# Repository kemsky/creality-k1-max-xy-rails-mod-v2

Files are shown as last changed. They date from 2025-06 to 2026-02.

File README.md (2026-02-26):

# Creality `K1 Max` XY Rails Mod V2

## Description

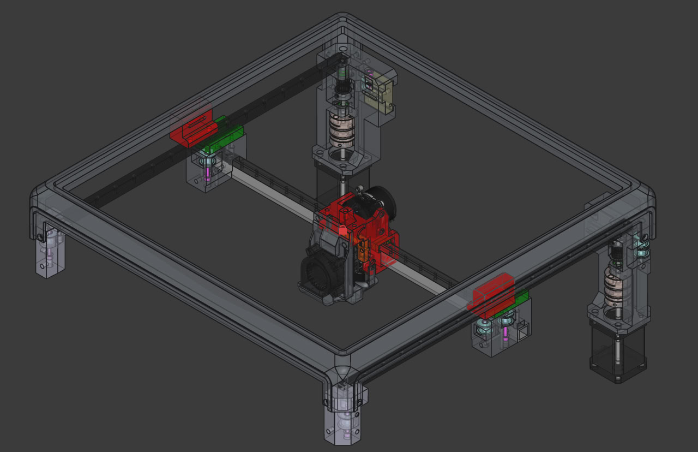
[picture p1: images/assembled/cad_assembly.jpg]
CAD


The primary difference from the previous version is MGN9 rail on X axis, it makes X axis lighter and increases maximum accelerations. Also, it includes all improvements made for regular K1.

This mod fixes `K1 Max` issues namely excessive ringing/echo, unstable print quality, frequent maintenance, also it makes printer quiet.

- **This mod does not change print area (almost, clr_noz_start_y: 297)**
- **You must use camera mount from this mod**
- **You must remove stock motor pulleys (or use non-stock stepper motors)**

### Belts, pulleys, motors

This mode uses `POWGE` 7.7 mm belt and corresponding idler pulleys. You can use 6 mm belt and stock idlers if you add washers to compensate height differences (`POWGE` idlers have 10.4 mm height). Also, you can use `F604ZZ` flanged bearings (4x12x4) and 2mm washers instead of `POWGE` pulleys.

You have to remove stock motor pulleys. You can use a bearing puller to do that (some people use printed pullers e.g. [pulley puller](https://www.printables.com/model/515503-pulley-puller)). If pulleys sit too tight you can use dremel and make cuts to relax pulleys. you have to be careful to avoid damage to motor shafts

I used 20T motor pulleys for 15 mm belt (`rotation_distance` needs to be adjusted to `40` and `driver_SGTHRS` must be tuned `printer.cfg`).

You can install non-stock motors e.g. `Leadshine 42cm06 1.8` (low VFA, silent, high torque, custom wiring needed) or `LDO-42STH48-1684MAC 0.9` (requires `full_steps_per_rotation: 400`, loud, limited acceleration, low VFA).

<details>
    <summary>Leadshine 42cm06 1.8 wiring</summary>
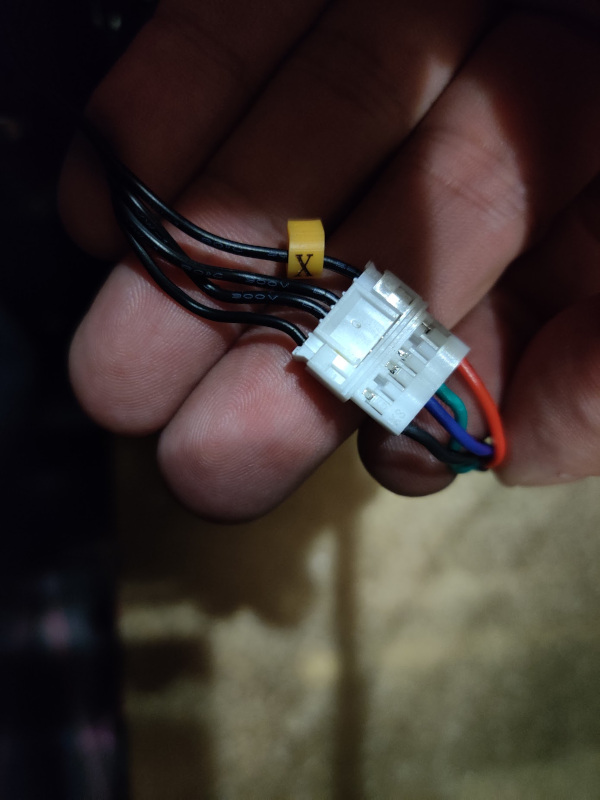
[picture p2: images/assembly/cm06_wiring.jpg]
    
</details>
<br>

This mod uses double diaphragm couplers and `MF95ZZ` bearings.

#### Belts tuning

Preferred way is to use Spectroid android app (or any other program that can show sound frequency).

Move toolhead to the middle, move X axis to have 150mm between motor mounts and XY joints.

Pluck the shortest belt on each side, displayed frequency should be the same. Target frequency is 120-130Hz, if you go higher than 130Hz you risk to damage belts.

#### Linear rails

This mod uses two `MGN12` rails with `MGN12H` carriages for Y and one `MGN9` rail with `MGN9H` carriage for X axis.

X rail has max length of 410 mm, 380 mm between far left and far right holes. X axis requires 15x15x2 mm aluminium tube (the same length as rail). It is important to use quality rails for X axis (with minimal backlash, Z1 preload).

Y rails have max length of 385 mm (375 + 5x2 mm), 375 mm between far left and far right holes.

#### Materials

Recommended printing materials are PA-GF, PA-CF, ABS-GF, ABS-CF or anything else that is rigid and can sustain high temperatures. Screw joints tend to become loose in ABS over time.

Wall loops, top/bottom layers should be at least 5, I'd recommend 6-7, infill 40%, add manual normal supports.

<details>
    <summary>Printing orientation</summary>
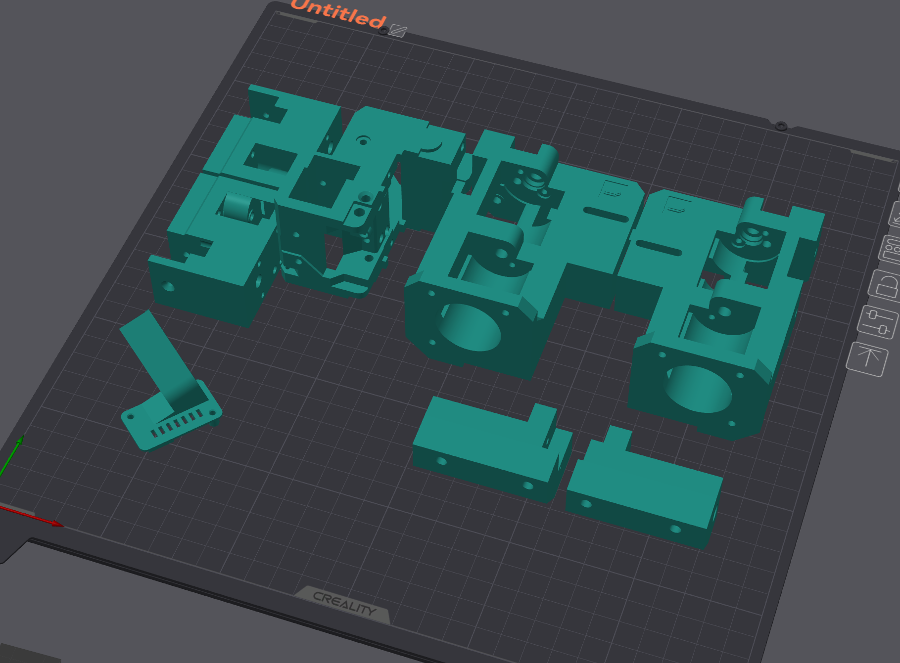
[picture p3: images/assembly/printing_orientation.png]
    
</details>

#### Options for maximum performance

- Use light extruder - [KKm extruder](https://www.printables.com/model/906070-artis3d-kkm-extruder-remix)

## License

All work in this repository falls under the Attribution-NonCommercial-ShareAlike 4.0 International (CC BY-NC-SA 4.0).

<https://creativecommons.org/licenses/by-nc-sa/4.0/>

### Notes

Partially this work is based on [creality-k1-xy-rails-mod](https://github.com/kemsky/creality-k1-xy-rails-mod) and uses some CAD files made by [Henlor](https://www.printables.com/@Henlor).

## Published

<https://www.printables.com/model/1339635-creality-k1-max-xy-linear-rails-mod-v2>

<!-- 
https://www.thingiverse.com/thing:6893994

https://makerworld.com/en/models/931135 -->

## Photos

<details>
    <summary>Photo 1</summary>
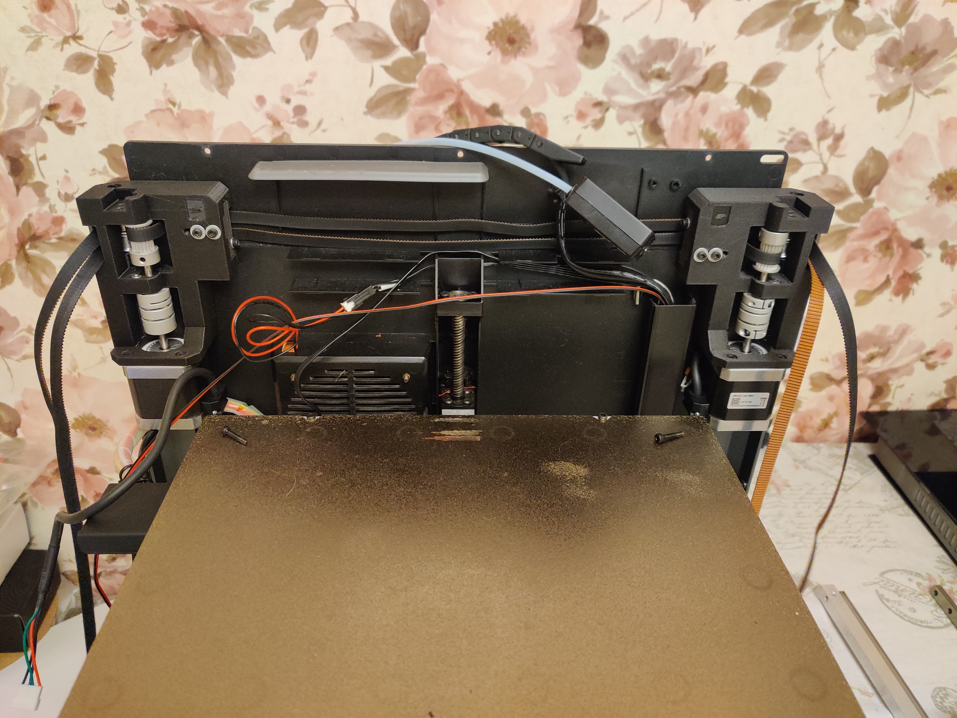
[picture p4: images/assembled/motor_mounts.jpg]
    
</details>

<details>
    <summary>Photo 2</summary>
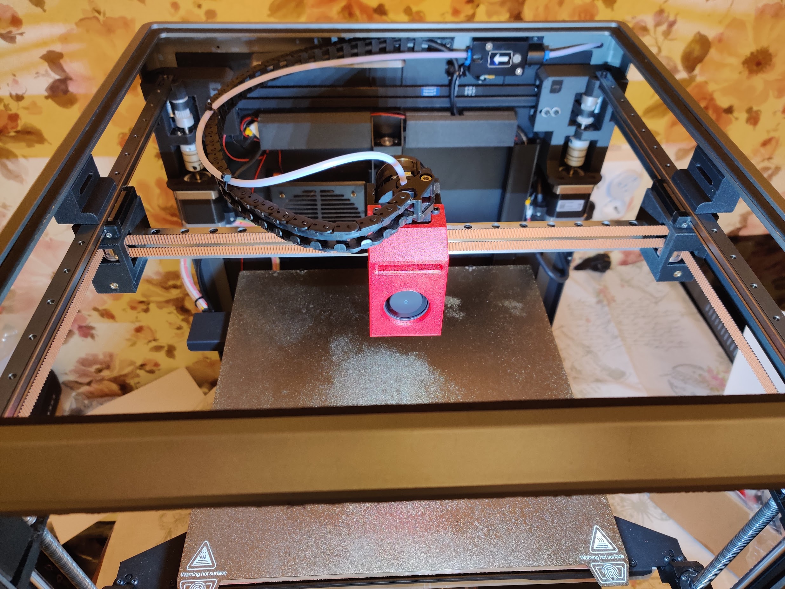
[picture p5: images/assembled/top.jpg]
    
</details>

## BOM, Assembly

! `Flat Thin Wafer Head Screw` - M3 screws with flat head that has 1 mm thickness.
You can find those on AliExpress, manufacturer NINDEJIN, search for "Ultra Low Profile Head Screw".

### Camera

<details>
    <summary>Preview</summary>
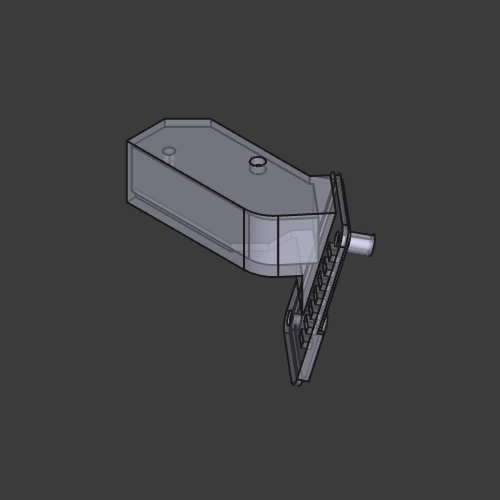
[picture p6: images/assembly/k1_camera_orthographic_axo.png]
k1_camera.stl
    
</details>
<br>

[k1_camera.stl](/stl/k1_camera.stl)

### Front idler left

<details>
    <summary>Preview</summary>
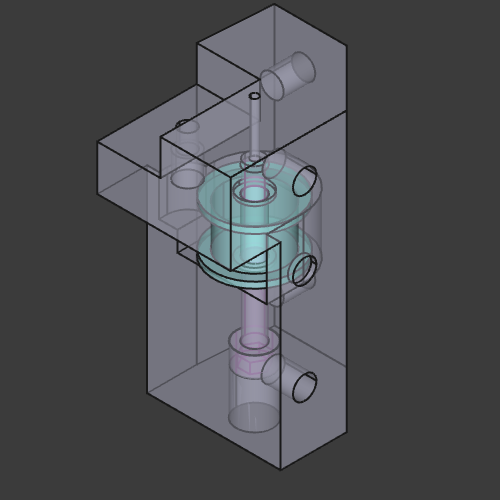
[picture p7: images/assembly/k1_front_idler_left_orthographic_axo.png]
front_idler_left.stl
    
</details>
<br>

[front_idler_left.stl](/stl/k1_front_idler_left.stl)

| Item | Type | Count |
|---|---|---|
| DIN 912 Socket Head Cap Screw | M4 30 mm  | 1 |
| DIN 7991 Flat Head Cap Screw | M3 6 mm | 4 |
| DIN 912 Socket Head Cap Screw | M3 16 mm  | 1 |
| POWGE GT2 No Teeth Idler Pulley | 7.7 mm | 1 |
| Heat insert | M3 5x5 mm | 5 |

### Front idler right

<details>
    <summary>Preview</summary>
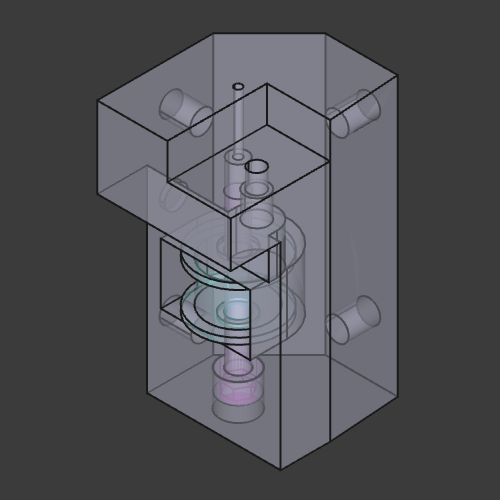
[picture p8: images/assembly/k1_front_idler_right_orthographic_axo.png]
front_idler_right.stl
    
</details>
<br>

[front_idler_right.stl](/stl/k1_front_idler_right.stl)

| Item | Type | Count |
|---|---|---|
| DIN 912 Socket Head Cap Screw | M4 30 mm  | 1 |
| DIN 7991 Flat Head Cap Screw | M3 6 mm | 4 |
| DIN 912 Socket Head Cap Screw | M3 16 mm  | 1 |
| POWGE GT2 No Teeth Idler Pulley | 7.7 mm | 1 |
| Heat insert | M3 5x5 mm | 5 |

### Joint left

<details>
    <summary>Preview</summary>
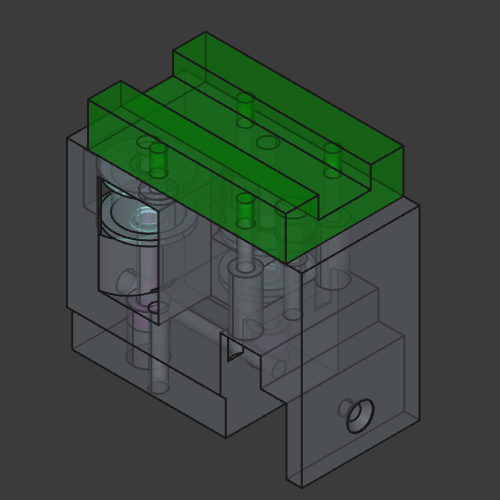
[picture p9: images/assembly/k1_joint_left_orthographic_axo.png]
k1_joint_left.stl
    
</details>
<br>

[k1_joint_left.stl](/stl/k1_joint_left.stl)

| Item | Type | Count |
|---|---|---|
| DIN 912 Socket Head Cap Screw | M4 30 mm | 2 |
| DIN 7991 Flat Head Cap Screw | M3 52 mm | 1 |
| Flat Thin Wafer Head Screw | M3 6 mm | 1 |
| DIN 912 Socket Head Cap Screw | M3 12 mm | 3 |
| DIN 912 Socket Head Cap Screw | M3 25 mm | 1 |
| POWGE GT2 No Teeth Idler Pulley | 7.7 mm | 2 |
| MGN12H block | | 1 |
| Heat insert | M3 4.5x5 mm | 1 |
| Heat insert | M3 5x7 mm | 1 |

### Joint right

<details>
    <summary>Preview</summary>
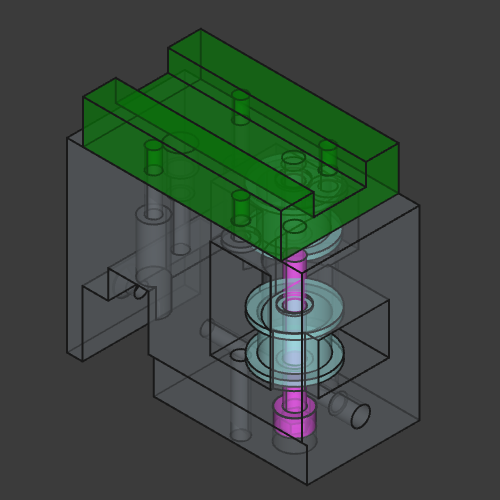
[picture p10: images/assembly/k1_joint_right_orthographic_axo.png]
k1_joint_right.stl
    
</details>
<br>

[k1_joint_right.stl](/stl/k1_joint_right.stl)

| Item | Type | Count |
|---|---|---|
| DIN 912 Socket Head Cap Screw | M4 30 mm | 2 |
| DIN 7991 Flat Head Cap Screw | M3 52 mm | 1 |
| Flat Thin Wafer Head Screw | M3 6 mm | 2 |
| DIN 912 Socket Head Cap Screw | M3 12 mm | 2 |
| DIN 912 Socket Head Cap Screw | M3 25 mm | 1 |
| POWGE GT2 No Teeth Idler Pulley | 7.7 mm | 2 |
| MGN12H block | | 1 |
| Heat insert | M3 4.5x5 mm | 1 |
| Heat insert | M3 5x7 mm | 1 |

### Y rail mounts

<details>
    <summary>Preview</summary>
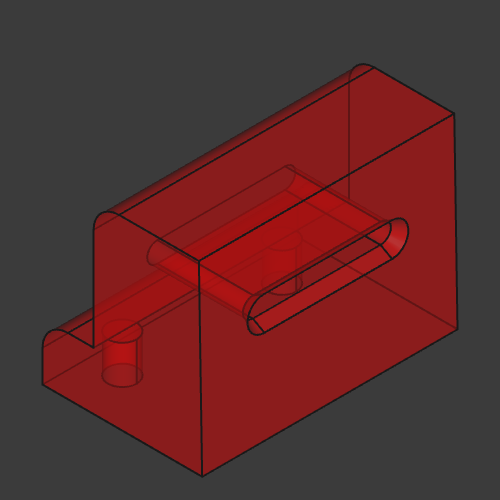
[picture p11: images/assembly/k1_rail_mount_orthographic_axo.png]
k1_rail_mount.stl
    
</details>
<br>

[k1_rail_mount.stl](/stl/k1_rail_mount.stl) x2

| Item | Type | Count |
|---|---|---|
| DIN 912 Socket Head Cap Screw | M3 25 mm  | 2 |
| DIN 912 Socket Head Cap Screw | M3 8 mm | 4 |
| Heat insert | M3 5x5 mm | 4 |

Mounting Y rails to the top frame is important if you want less vibrations.

### Y axis

See [cad_rail_mgn12.FCStd](/src/cad_rail_mgn12.FCStd) for exact configuration and dimensions.

| Item | Type | Count |
|---|---|---|
| MGN12 linear rail | 385 mm | 2 |

Y rails have max length of 385 mm (375 + 5x2 mm), 375 mm between far left and far right holes. `MGN12H` carriage.

### X axis

See [cad_x_axis.FCStd](/src/cad_x_axis.FCStd) for exact configuration and dimensions.

First, make two holes on the left and on the right, tap M3 threads, mount MGN9 rail, align it carefully and tighten screws. Use rail as drilling template, make mark using 4 mm drill bit, then drill remaining holes using 2.5 mm drill bit, then tap M3 threads.

| Item | Type | Count |
|---|---|---|
| Aluminium square pipe | 15x15x2 410 mm | 1 |
| DIN 912 Socket Head Cap Screw | M3 6 mm | 9-18  |
| MGN9 linear rail | 410 mm | 1 |

X rail has max length of 410 mm, 380 mm between far left and far right holes. X axis requires 15x15x2 mm aluminium tube (the same length as rail). `MGN9H` carriage.

It is important to use quality rails for X axis (with minimal backlash, Z1 preload).

### Tensioner left

<details>
    <summary>Preview</summary>
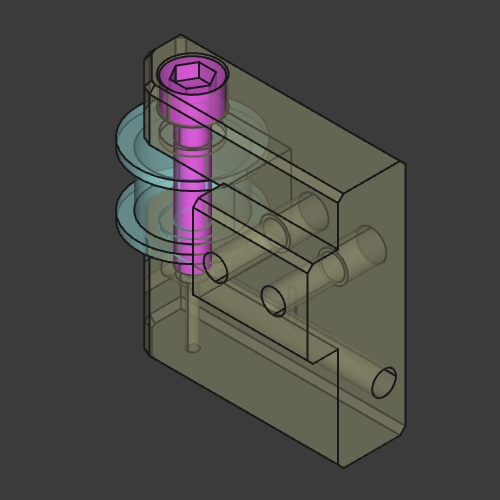
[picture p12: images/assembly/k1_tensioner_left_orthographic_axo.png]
k1_tensioner_left.stl
    
</details>
<br>

[k1_tensioner_left.stl](/stl/k1_tensioner_left.stl)

| Item | Type | Count |
|---|---|---|
| DIN 912 Socket Head Cap Screw | M3 45 mm | 1 |
| DIN 912 Socket Head Cap Screw | M3 16 mm | 2 |
| DIN 912 Socket Head Cap Screw | M4 20 mm | 1 |
| Washer/Gasket | M3 | 2 |
| POWGE GT2 No Teeth Idler Pulley | 7.7 mm | 1 |
| Heat insert | M3 4.5x3 mm | 2 |

### Tensioner right

<details>
    <summary>Preview</summary>
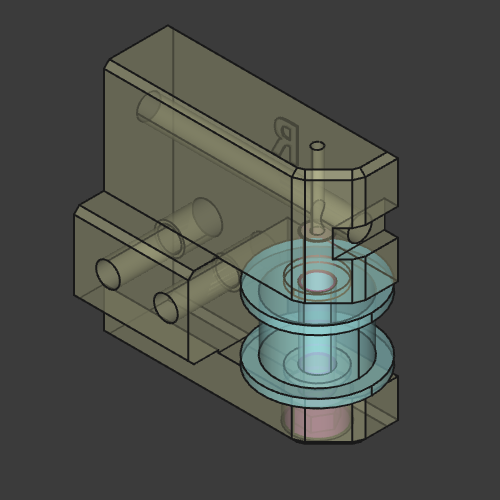
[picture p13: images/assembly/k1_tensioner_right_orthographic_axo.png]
k1_tensioner_right.stl
    
</details>
<br>

[k1_tensioner_right.stl](/stl/k1_tensioner_right.stl)

| Item | Type | Count |
|---|---|---|
| DIN 912 Socket Head Cap Screw | M3 45 mm | 1 |
| DIN 912 Socket Head Cap Screw | M3 16 mm | 2 |
| DIN 912 Socket Head Cap Screw | M4 20 mm | 1 |
| Washer/Gasket | M3 | 2 |
| POWGE GT2 No Teeth Idler Pulley | 7.7 mm | 1 |
| Heat insert | M3 4.5x3 mm | 2 |

### Motor mount left

<details>
    <summary>Preview</summary>
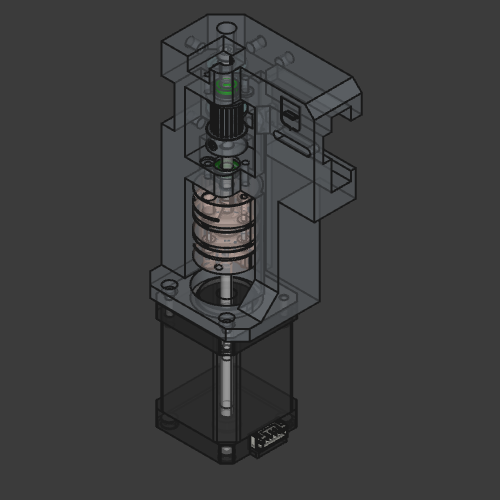
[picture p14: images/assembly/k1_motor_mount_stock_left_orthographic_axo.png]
k1_motor_mount_stock_left.stl
    
</details>
<br>

- For stock motors - [k1_motor_mount_stock_left.stl](/stl/k1_motor_mount_stock_left.stl)
- For non-stock motors - [k1_motor_mount_left.stl](/stl/k1_motor_mount_left.stl)

| Item | Type | Count |
|---|---|---|
| DIN 7991 Flat Head Cap Screw | M3 6 mm | 4 |
| DIN 912 Socket Head Cap Screw | M3 6 mm | 3 |
| DIN 912 Socket Head Cap Screw | M3 16 mm  | 1 |
| Flat Thin Wafer Head Screw | M3 6 mm | 2 |
| MF95ZZ Bearing | | 2 |
| Double Diaphragm Coupler | 20x30 5x5 | 1 |
| Shaft | 5x57 mm | 1 |
| Motor Pulley for 15mm belt | 20T 5 mm  | 1 |
| POWGE GT2 No Teeth Idler Pulley | 7.7 mm | 2 |
| Heat insert | M3 5x5 mm | 6 |

You'll need 1 M3x35 screw from stock gantry motor mounts and 1 M3 5x7 mm heat insert, alternatively you can use M4x35 SHCS screw.

### Motor mount right

<details>
    <summary>Preview</summary>
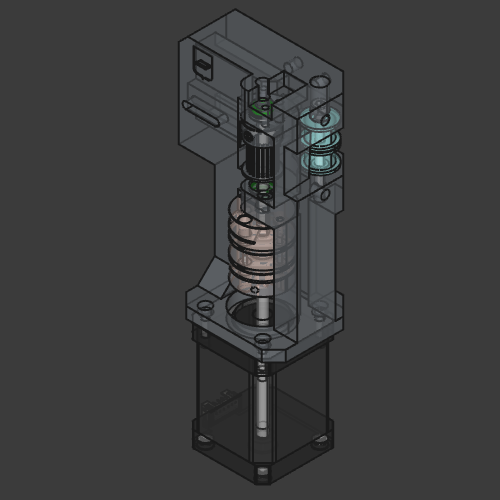
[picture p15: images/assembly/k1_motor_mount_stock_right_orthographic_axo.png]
k1_motor_mount_stock_right.stl
    
</details>
<br>

- For stock motors - [k1_motor_mount_stock_right.stl](/stl/k1_motor_mount_stock_right.stl)
- For non-stock motors - [k1_motor_mount_right.stl](/stl/k1_motor_mount_right.stl)

| Item | Type | Count |
|---|---|---|
| DIN 7991 Flat Head Cap Screw | M3 6 mm | 4 |
| DIN 912 Socket Head Cap Screw | M3 6 mm | 3 |
| DIN 912 Socket Head Cap Screw | M3 16 mm  | 1 |
| Flat Thin Wafer Head Screw | M3 6 mm | 2 |
| MF95ZZ Bearing | | 2 |
| Double Diaphragm Coupler | 20x30 5x5 | 1 |
| Shaft | 5x57 mm | 1 |
| Motor Pulley for 15mm belt | 20T 5 mm  | 1 |
| POWGE GT2 No Teeth Idler Pulley | 7.7 mm | 2 |
| Heat insert | M3 5x5 mm | 6 |

You'll need 1 M3x35 screw from stock gantry motor mounts and 1 M3 5x7 mm heat insert, alternatively you can use M4x35 SHCS screw.

### Toolhead clamp left

<details>
    <summary>Preview</summary>
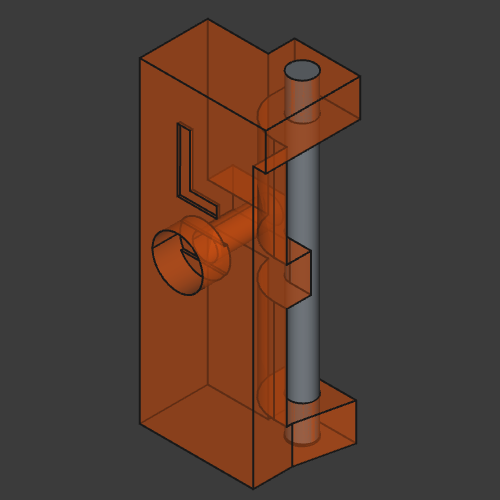
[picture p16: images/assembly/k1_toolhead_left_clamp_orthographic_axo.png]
k1_toolhead_left_clamp.stl
    
</details>
<br>

[k1_toolhead_left_clamp.stl](/stl/k1_toolhead_left_clamp.stl)

| Item | Type | Count |
|---|---|---|
| DIN 912 Socket Head Cap Screw | M2 10 mm | 1 |
| Shaft | 2x25 mm | 1 |

### Toolhead clamp right

<details>
    <summary>Preview</summary>
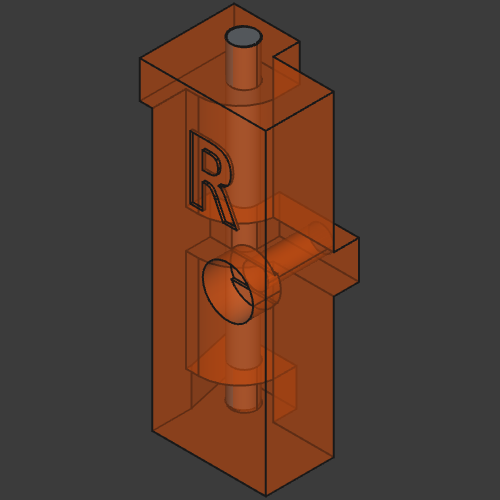
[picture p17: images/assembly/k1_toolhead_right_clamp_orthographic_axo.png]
k1_toolhead_right_clamp.stl
    
</details>
<br>

[k1_toolhead_right_clamp.stl](/stl/k1_toolhead_right_clamp.stl)

| Item | Type | Count |
|---|---|---|
| DIN 912 Socket Head Cap Screw | M2 10 mm | 1 |
| Shaft | 2x25 mm | 1 |

### Toolhead fan spacer

<details>
    <summary>Preview</summary>
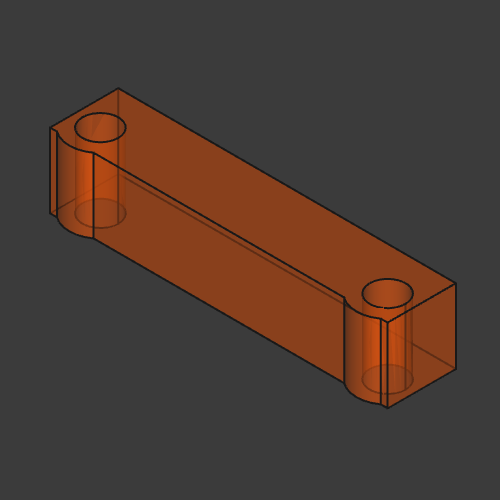
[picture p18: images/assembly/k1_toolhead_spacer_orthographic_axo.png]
k1_toolhead_spacer.stl
    
</details>
<br>

Regular hotend - [k1_toolhead_spacer.stl](/stl/k1_toolhead_spacer.stl)

Unicorn hotend - [k1_toolhead_spacer_unicorn.stl](/stl/k1_toolhead_spacer_unicorn.stl)

### Toolhead

<details>
    <summary>Preview</summary>
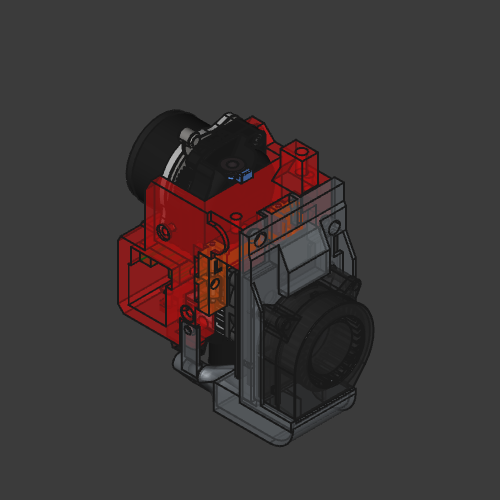
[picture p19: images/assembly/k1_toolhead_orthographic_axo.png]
k1_toolhead.stl
    
</details>
<br>

[k1_toolhead.stl](/stl/k1_toolhead.stl)

| Item | Type | Count |
|---|---|---|
| Flat Thin Wafer Head Screw | M3 6 mm | 4 |
| Flat Thin Wafer Head Screw | M3 8 mm | 3 |
| DIN 912 Socket Head Cap Screw | M2 12 mm | 1 |
| MGN9H block | | 1 |
| Heat insert | M3 4.5x3 mm | 6 |
| Heat insert | M3 5x7 mm | 1 |
| Heat insert | M3 5x4 mm | 4 |
| Heat insert | M2 3.5x3 mm | 4 |

#### Toolhead Microprobe

| Item | Type | Count |
|---|---|---|
| Heat insert | M2.5 3.5x4 mm | 2 |

You can install `BIQU MicroProbe` sensor which is much better than original load cell probe.

[ **!** ] Pins on toolhead board ("touch" connector) do not match microprobe pins, you can not use premade JST 1.25 5pins cable, you'll have to make your own.

<details>
    <summary>Pins</summary>
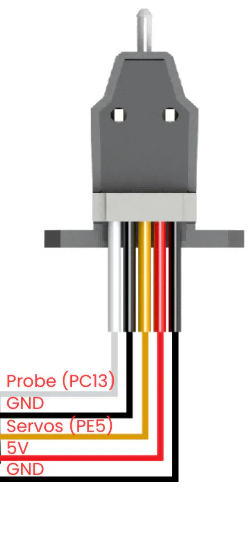
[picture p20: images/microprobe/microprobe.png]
microprobe
    
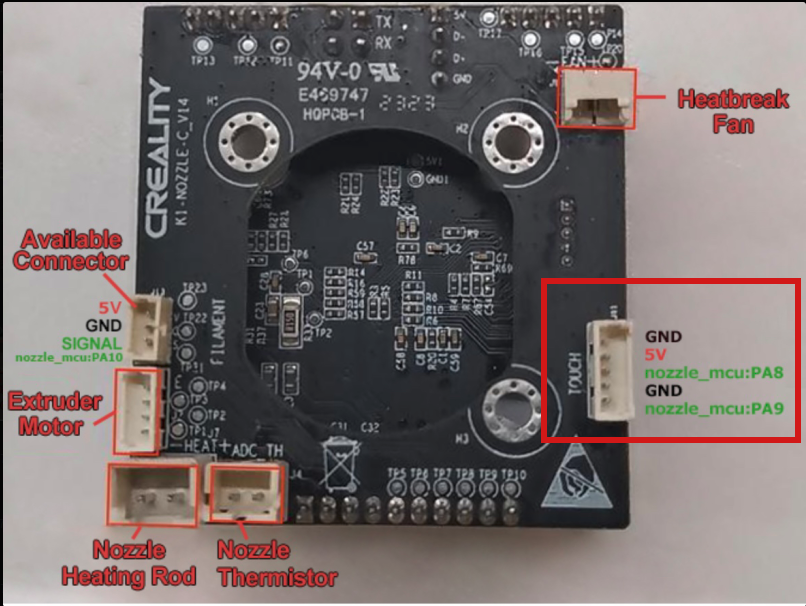
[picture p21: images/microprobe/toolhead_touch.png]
toolhead_touch
    
</details>
<br>

```pre
- touch GND            -> microprobe GND    (black)
- touch 5v             -> microprobe 5v     (red)
- touch nozzle_mcu:PA8 -> microprobe servo  (yellow)
- touch GND            -> microprobe GND    (black)
- touch nozzle_mcu:PA9 -> microprobe probe  (white)
```

1. Remove all `prtouch` sections from `printer.cfg`
2. Edit `/usr/share/klipper/klippy/extras/custom_macro.py` and comment all prtouch usages
3. Remove `/usr/share/klipper/klippy/extras/custom_macro.pyc` and reboot
4. Add the following to `printer.cfg`:

    ```cfg
    [gcode_macro _PROBE_DOWN]
    gcode:
        SET_PIN PIN=probe_enable VALUE=1

    [gcode_macro _PROBE_UP]
    gcode:
        SET_PIN PIN=probe_enable VALUE=0

    [output_pin probe_enable]
    pin: nozzle_mcu:PA8
    value: 0

    [probe]
    pin: ^!nozzle_mcu:PA9
    deactivate_on_each_sample: False
    x_offset: 0
    y_offset: 20
    z_offset: 0  # do PROBE_CALIBRATE
    samples: 2
    samples_tolerance: 0.05
    samples_tolerance_retries: 3
    activate_gcode:
        _PROBE_DOWN
        G4 P500
    deactivate_gcode:
        _PROBE_UP
    ```

5. Modify `[stepper_z]` section in `printer.cfg`, set `endstop_pin` to `probe:z_virtual_endstop`
6. Use `PROBE_CALIBRATE` macros to determine Z-Offset and save it.
7. Sometimes you can get error `Communication Timeout during homing z`. Use `vi /usr/share/klipper/klippy/mcu.py` and increase `TRSYNC_TIMEOUT` from 0.025 up to 0.05. Remove file `/usr/share/klipper/klippy/mcu.pyc`, reboot.

Depending on your hotend you may need a spacer.

<details>
    <summary>Microprobe spacer</summary>
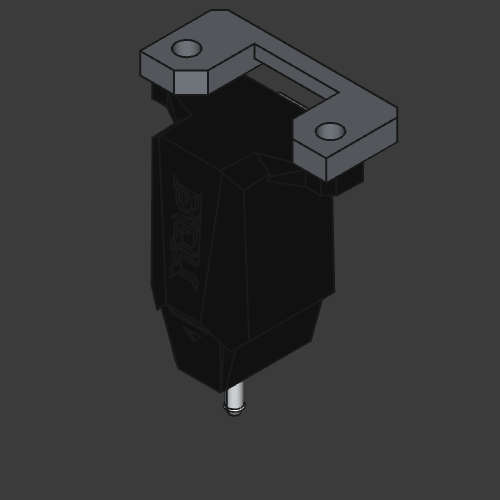
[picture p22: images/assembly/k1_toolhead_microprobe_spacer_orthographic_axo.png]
k1_toolhead_microprobe_spacer.stl
    
</details>
<br>

[k1_toolhead_microprobe_spacer.stl](/stl/k1_toolhead_microprobe_spacer.stl)

## Bonus Models

### Toolhead cover

<details>
    <summary>Preview</summary>
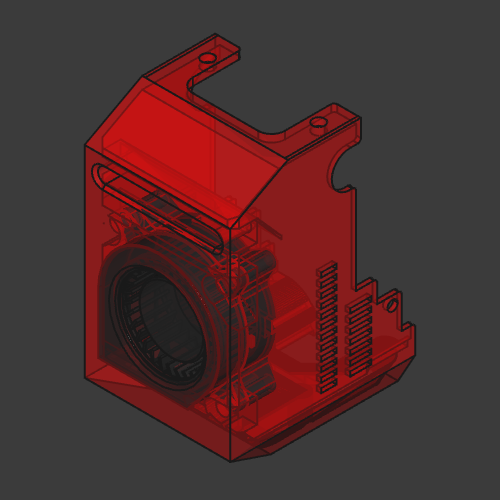
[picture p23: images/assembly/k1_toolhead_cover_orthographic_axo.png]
k1_toolhead_cover.stl
    
</details>
<br>

[k1_toolhead_cover.stl](/stl/k1_toolhead_cover.stl)

### Compact toolhead cover

<details>
    <summary>Preview</summary>
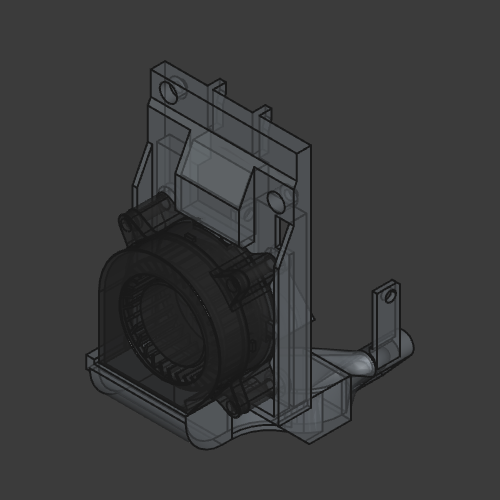
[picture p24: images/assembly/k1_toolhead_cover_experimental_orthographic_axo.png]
k1_toolhead_cover_experimental.stl
    
</details>
<br>

[k1_toolhead_cover_experimental.stl](/stl/k1_toolhead_cover_experimental.stl)

### Cable cover

<details>
    <summary>Preview</summary>
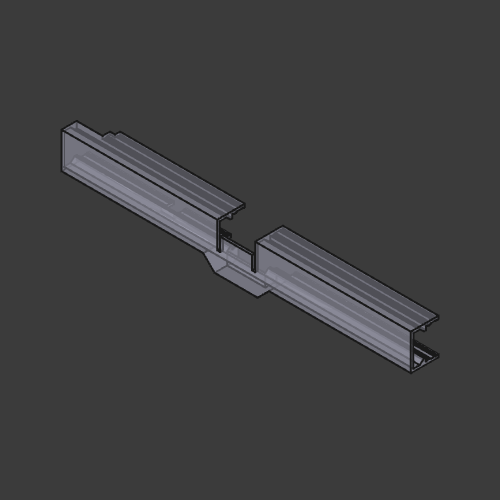
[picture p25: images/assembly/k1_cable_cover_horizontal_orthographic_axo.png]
k1_cable_cover_horizontal_orthographic_axo
    
</details>
<br>

Horizontal - [k1_cable_cover_horizontal.stl](/stl/k1_cable_cover_horizontal.stl)

### Z-Carriage for T8 Oldham Coupler

<details>
    <summary>Preview</summary>
    k1_z_carriage_oldham.stl
</details>
<br>

[k1_z_carriage_oldham.stl](/stl/k1_z_carriage_oldham.stl)

### Side fan duct

<details>
    <summary>Preview</summary>
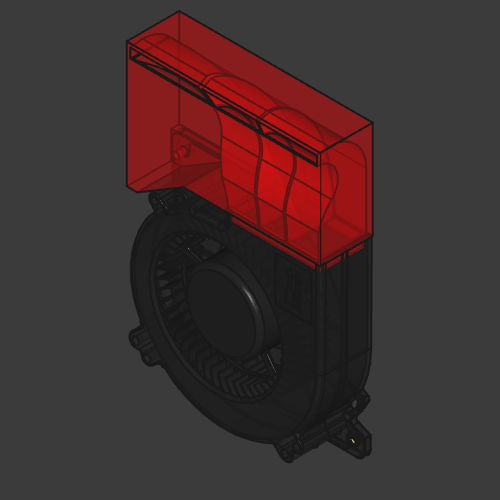
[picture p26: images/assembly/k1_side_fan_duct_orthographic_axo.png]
k1_side_fan_duct.stl
    
</details>
<br>

[k1_side_fan_duct.stl](/stl/k1_side_fan_duct.stl)

### Cutter block

Requires 2x25mm DIN 912 M3 screws.

<details>
    <summary>Preview</summary>
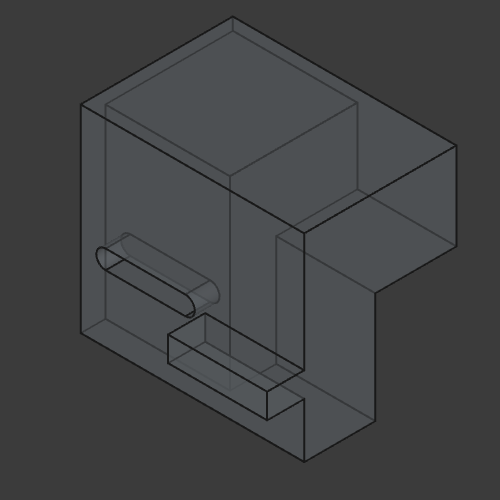
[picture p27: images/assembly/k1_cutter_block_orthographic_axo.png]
k1_cutter_block.stl
    
</details>
<br>

[k1_cutter_block.stl](/stl/k1_cutter_block.stl)

There is hopper block as well but it is not tested, see issue [#7](https://github.com/kemsky/creality-k1-max-xy-rails-mod-v2/issues/7).

### Mellow Fly Mini Pad

This is part of electronics upgrade.

Requires 4x5mm and 4x6mm DIN 912 M3 screws. 8 + 1 heat inserts. It also requires specific USB cable due to lack of space (you can make one yourself from donor cable).

<details>
    <summary>Preview</summary>
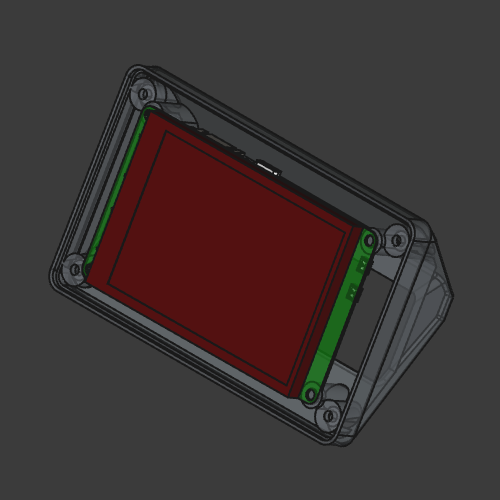
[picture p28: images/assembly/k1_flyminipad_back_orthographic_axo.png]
k1_flyminipad_back.stl
    
</details>
<br>

[k1_flyminipad_back.stl](/stl/k1_flyminipad_back.stl)

<details>
    <summary>Preview</summary>
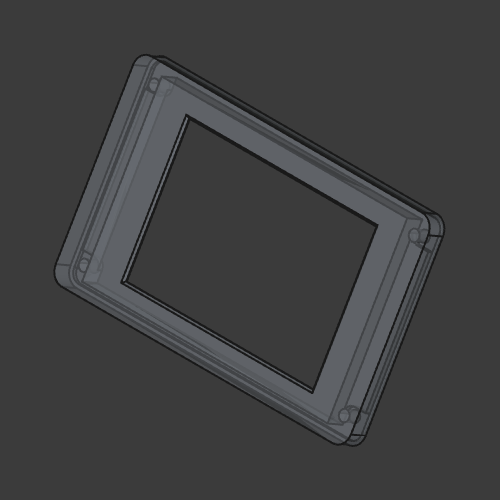
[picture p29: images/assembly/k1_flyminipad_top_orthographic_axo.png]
k1_flyminipad_top.stl
    
</details>
<br>

[k1_flyminipad_top.stl](/stl/k1_flyminipad_top.stl)

## Automation

`export.sh`/`export.cmd` scripts export all necessary objects to STl and STEP and optionally capture model screenshots.

```bash
# without updating screenshots:
./export.sh
# export STL, STEP and generate model screenshots:
./export.sh screenshots
```

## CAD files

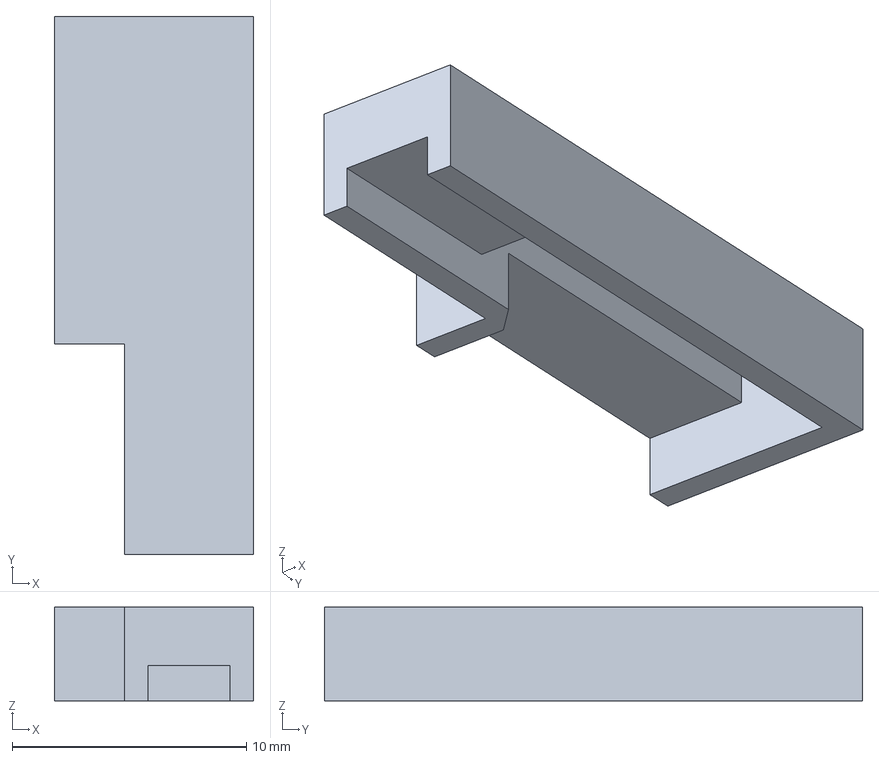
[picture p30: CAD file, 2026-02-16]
src/usb_connector_top.FCStd
8.50 x 23.0 x 4.00 mm

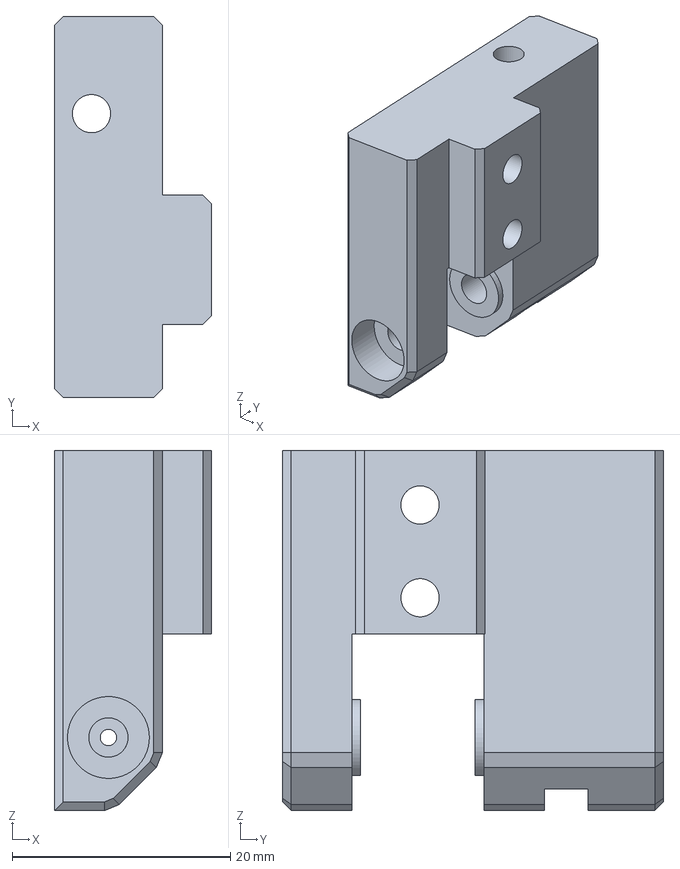
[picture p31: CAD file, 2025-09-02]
step/k1_tensioner_right.step
14.4 x 34.9 x 33.0 mm

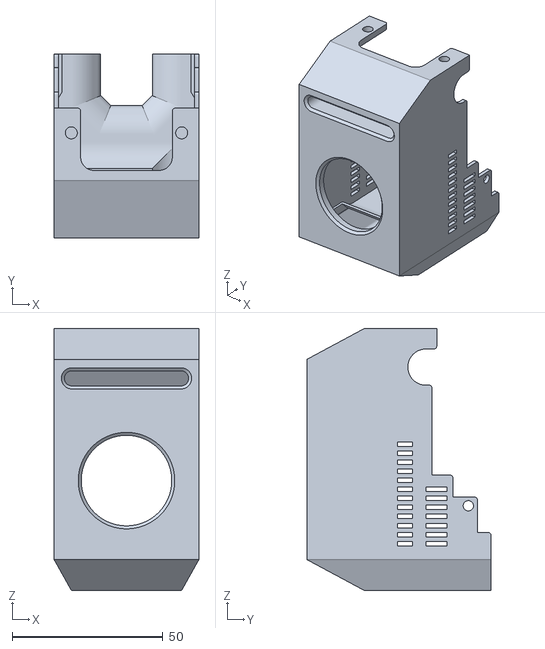
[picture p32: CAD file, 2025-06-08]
stl/k1_toolhead_cover.stl
48.0 x 61.0 x 86.9

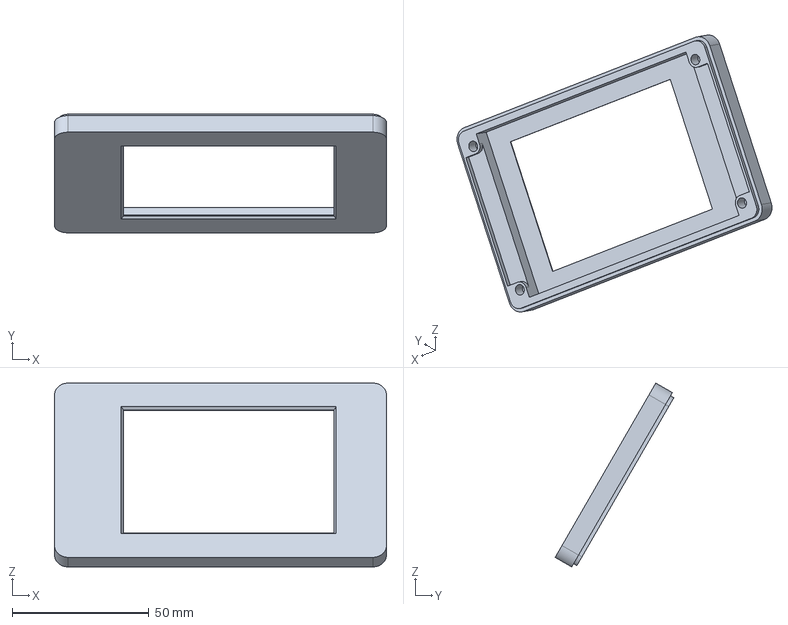
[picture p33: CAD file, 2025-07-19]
step/k1_flyminipad_top.step
121.4 x 43.4 x 67.2 mm

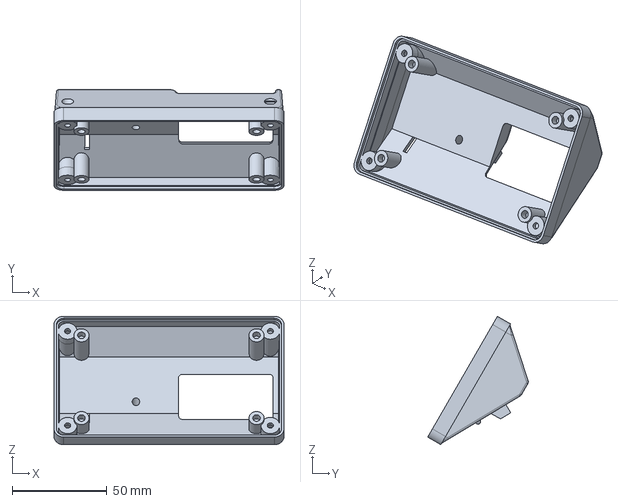
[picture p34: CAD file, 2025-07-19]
step/k1_flyminipad_back.step
121.4 x 53.1 x 67.7 mm

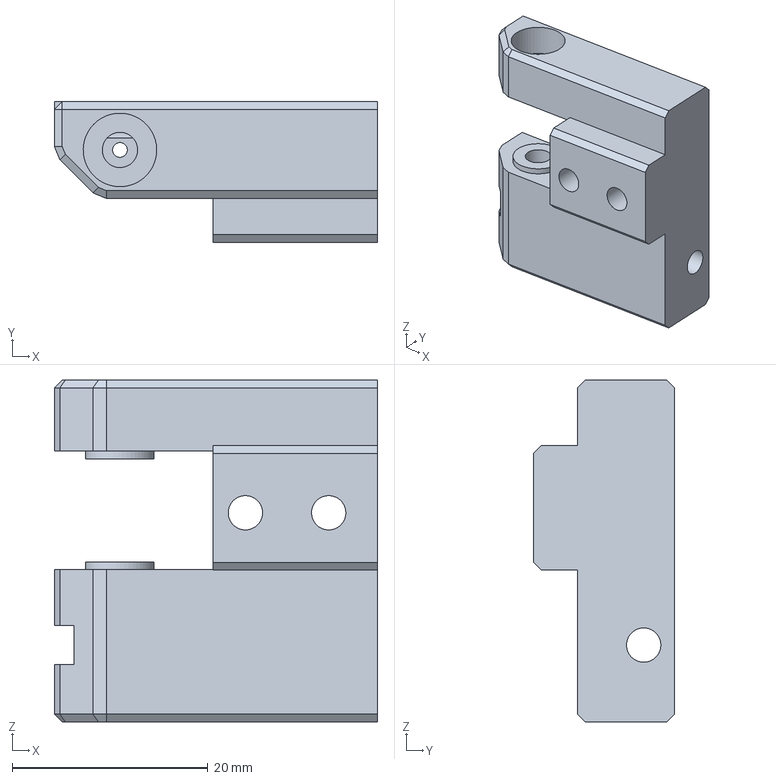
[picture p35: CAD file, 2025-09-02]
src/k1_tensioner_left.FCStd
33.0 x 14.4 x 34.9 mm

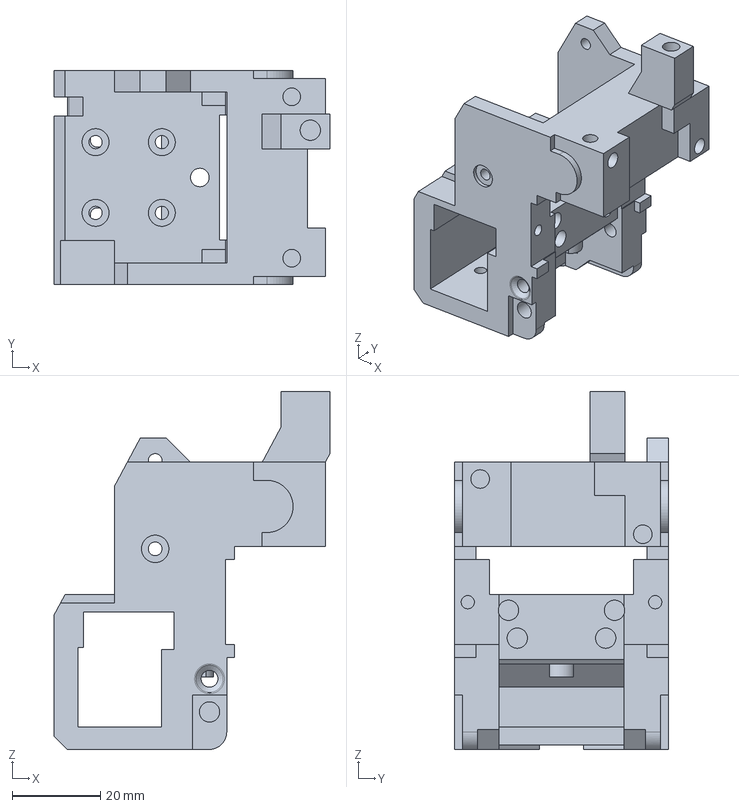
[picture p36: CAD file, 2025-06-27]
step/k1_toolhead.step
62.4 x 48.4 x 81.0 mm

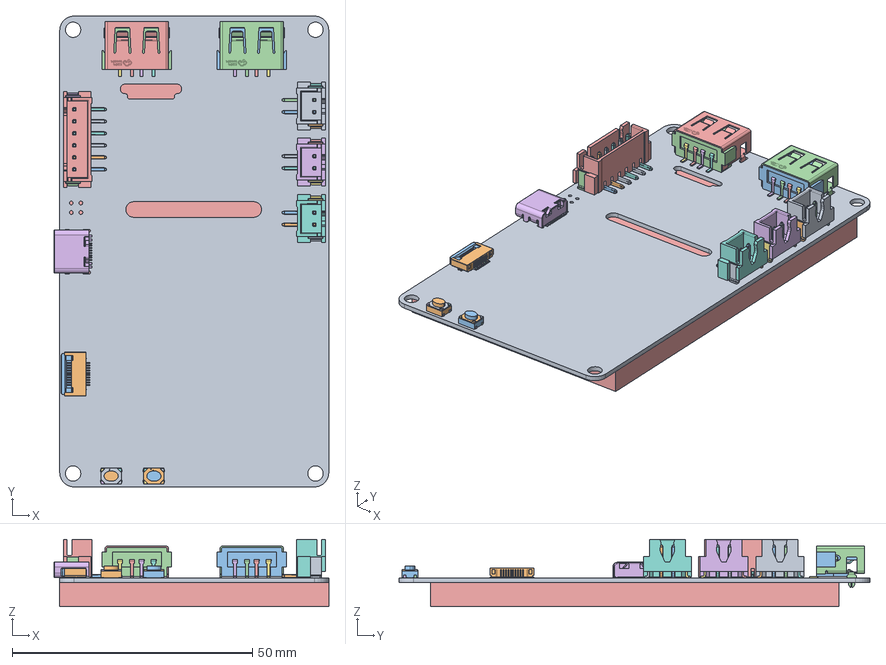
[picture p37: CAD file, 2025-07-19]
src/cad_flyminipad.FCStd
57.2 x 98.0 x 14.0 mm
SW-SMD_ST-1188U
SW-SMD_ST-1188U001
SW-SMD_ST-1188U002
SW-SMD_ST-1188U003
SW-SMD_ST-1188U004
SW-SMD_ST-1188U005
SW-SMD_ST-1188U006
SW-SMD_ST-1188U007
SW-SMD_ST-1188U008
SW-SMD_ST-1188U009
SW-SMD_ST-1188U010
SW-SMD_ST-1188U011
SW-SMD_ST-1188U012
SW-SMD_ST-1188U013
SW-SMD_ST-1188U014
SW-SMD_ST-1188U015
SW-SMD_ST-1188U016
SW-SMD_ST-1188U017
SW-SMD_ST-1188U018
SW-SMD_ST-1188U019
SW-SMD_ST-1188U020
SW-SMD_ST-1188U021
SW-SMD_ST-1188U022
SW-SMD_ST-1188U024
SW-SMD_ST-1188U025
SW-SMD_ST-1188U026
SW-SMD_ST-1188U027
SW-SMD_ST-1188U028
SW-SMD_ST-1188U029
SW-SMD_ST-1188U030
SW-SMD_ST-1188U031
SW-SMD_ST-1188U032
SW-SMD_ST-1188U033
SW-SMD_ST-1188U034
SW-SMD_ST-1188U035
SW-SMD_ST-1188U036
SW-SMD_ST-1188U037
SW-SMD_ST-1188U038
SW-SMD_ST-1188U039
SW-SMD_ST-1188U040
SW-SMD_ST-1188U041
SW-SMD_ST-1188U042
SW-SMD_ST-1188U043
SW-SMD_ST-1188U044
SW-SMD_ST-1188U045
SW-SMD_ST-1188U046
XH2.54-LS-2P
XH2.54-LS-2P001
XH2.54-LS-2P002
XH2.54-LS-ӽ½À
XH2.54-LS-ӽ½À001
LOGOԲ0.5
LOGOԲ0.069
LOGOԲ0.070
LOGOԲ0.071
LOGOԲ0.072
LOGOԲ0.073
LOGOԲ0.074
LOGOԲ0.075
LOGOԲ0.076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

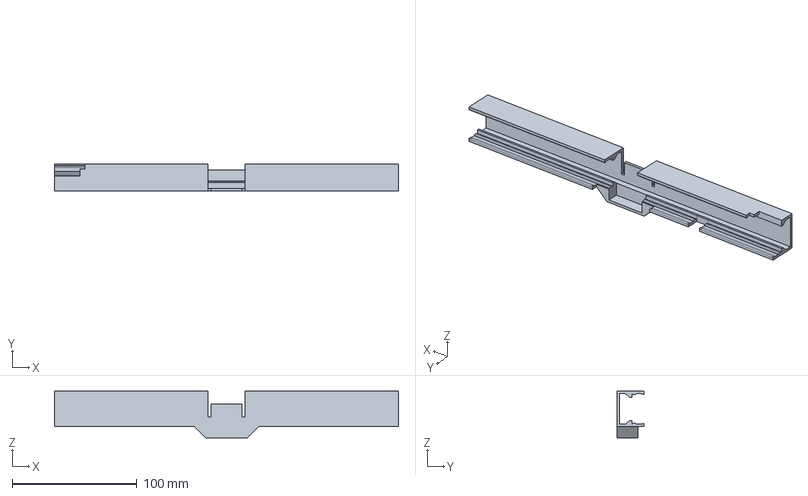
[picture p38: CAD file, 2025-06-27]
step/k1_cable_cover_horizontal.step
276.0 x 21.9 x 37.4 mm

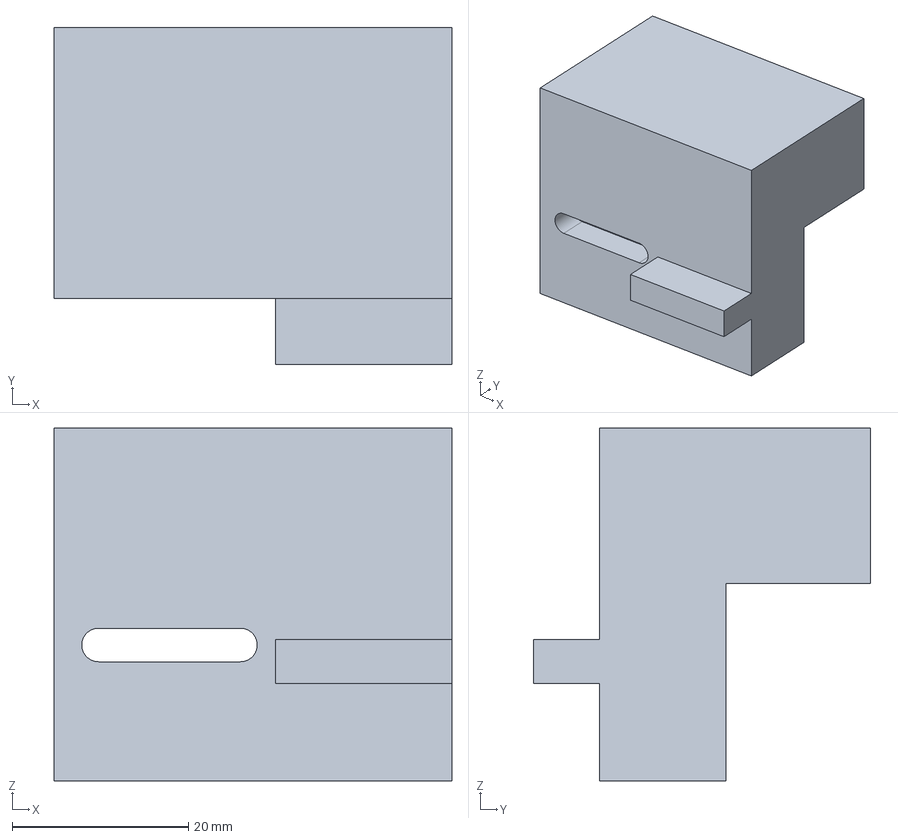
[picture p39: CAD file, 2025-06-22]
step/k1_cutter_block.step
45.2 x 38.3 x 40.0 mm

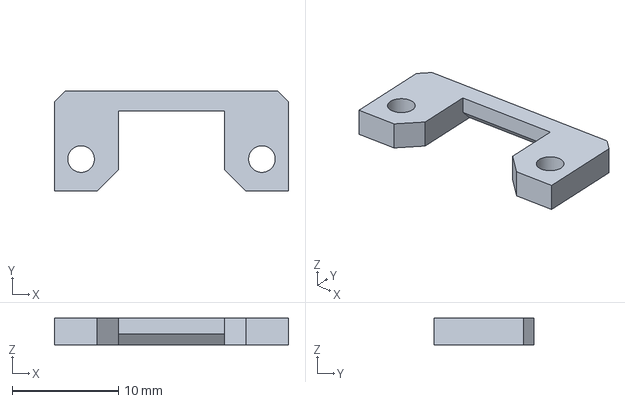
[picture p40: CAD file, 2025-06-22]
step/k1_toolhead_microprobe_spacer.step
22.0 x 9.40 x 2.50 mm

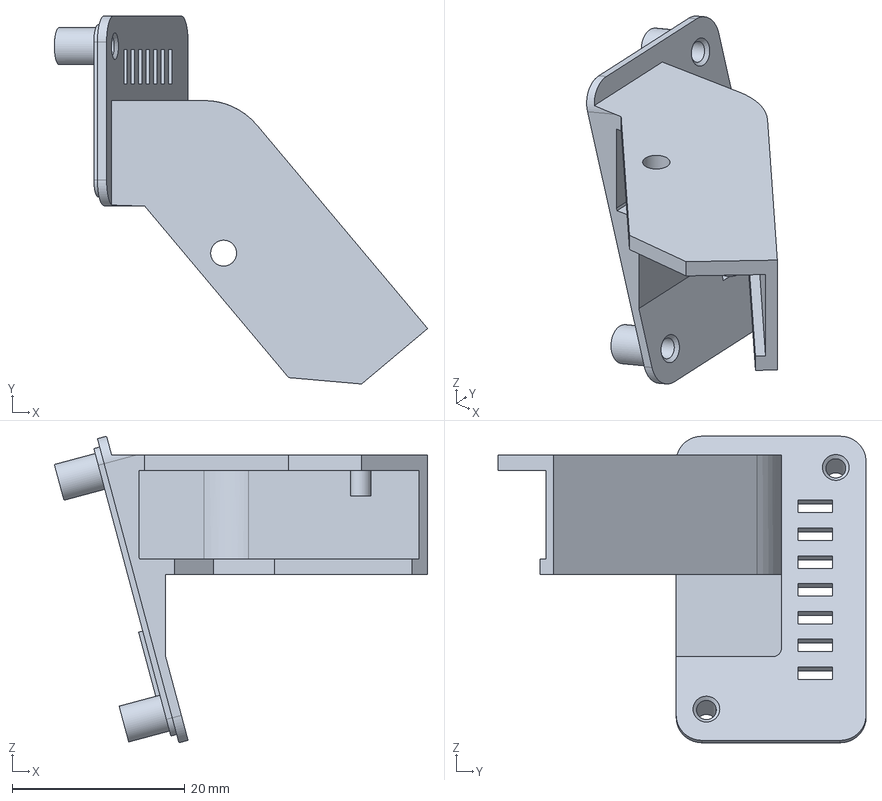
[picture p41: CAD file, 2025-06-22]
step/k1_camera.step
43.3 x 42.7 x 35.5 mm

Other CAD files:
src/cad_screen_assembly.FCStd
src/cad_assembly.FCStd
src/usb_connector_bottom.FCStd
src/k1_tensioner_right.FCStd
src/k1_flyminipad_top.FCStd
src/k1_flyminipad_back.FCStd
src/cad_15x15.FCStd
src/cad_20T_15mm_pulley.FCStd
src/cad_3010.FCStd
src/cad_4020.FCStd
src/cad_M4_DIN912_20mm.FCStd
src/cad_M4_DIN912_30mm.FCStd
src/cad_diaphragm_coupler.FCStd
src/cad_hotend.FCStd
src/cad_m4_35mm.FCStd
src/cad_mf95zz.FCStd
src/cad_mgn12h_block.FCStd
src/cad_mgn9h_block.FCStd
src/cad_motor_shaft_55mm.FCStd
src/cad_nema17_42_48.FCStd
src/cad_nema17_42_60.FCStd
src/cad_pcb.FCStd
src/cad_powge_pulley.FCStd
src/cad_rail_mgn12.FCStd
src/cad_rail_mgn9.FCStd
src/cad_shaft_2_25mm.FCStd
src/cad_top_frame.FCStd
src/cad_x_axis.FCStd
src/cad_x_gantry.FCStd
src/k1_cable_cover_horizontal.FCStd
src/k1_camera.FCStd
src/k1_cutter_block.FCStd
src/k1_front_idler_left.FCStd
src/k1_front_idler_right.FCStd
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

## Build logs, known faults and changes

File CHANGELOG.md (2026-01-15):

# Changelog

## 2026-01-15

- BOM fix

## 2025-12-29

- update microprobe docs

## 2025-09-02

- correct tensioners size
- add microprobe fix

## 2025-07-19

- correct Y rails size in the description
- added Mellow Fly Mini Pad case to replace stock screen

## 2025-06-28

- added printing orientation

## 2025-06-08

- initial commit

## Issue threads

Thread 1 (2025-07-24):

Tensioners size problem

Kirorus, 2025-07-24:
Is it normal for the left and right tensioners to be different heights? The corresponding parts seem to be the same height.

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

kemsky, 2025-09-02:
@Kirorus, fixed.

Closed 2025-09-02.

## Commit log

2025-06-28 printing orientation
2025-07-19 add fly mini pad case
    [cad_flyminipad.FCStd, cad_screen_assembly.FCStd, k1_flyminipad_back.FCStd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]
2025-09-02 correct tensioners size
    [k1_tensioner_left.FCStd, k1_tensioner_right.FCStd, k1_tensioner_right.step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]
2026-01-15 correct BOM
2026-02-16 add angled usb connector for Mellow Fly Mini Pad
    [usb_connector_bottom.FCStd, usb_connector_top.FCStd]
